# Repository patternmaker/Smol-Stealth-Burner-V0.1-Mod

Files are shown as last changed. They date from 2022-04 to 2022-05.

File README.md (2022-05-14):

# Smol-Stealth-Burner-V0.1-Mod
This Smol stealth burner does not lose any X,Y or Z travel. This means on stock V0.1 you don't need new bed mounts and you don't need to remove your stock bed. It has all best features I wanted in a Smol hotend without taking apart half your printer!
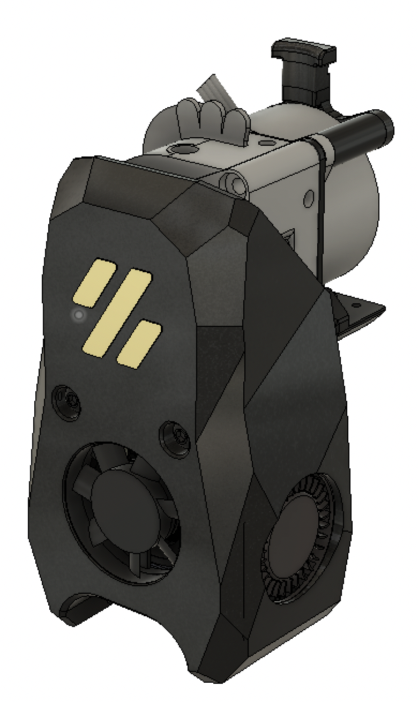
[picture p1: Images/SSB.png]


# License:
https://github.com/VoronDesign/Voron-0/blob/Voron0.1/LICENSE

I would say this is an intermediate build. You will need knowledge of soldering as well as wiring in general. You will need to work with small objects that can be a pain for unsteady hands. please keep this in mind.

# I AM NOT RESPONSIBLE FOR ANY DAMAGES TO YOUR PRINTER. PERFORM THIS MOD AT YOUR OWN RISK.

Print settings are standard Voron settings. The only exception is the X carraige. This will need support. There are two X carraige types. One with auto generated support and one without. I recommend printing the one without but if you don't trust your slicer use the one with. No way around it. You want the full x,y travel? Sacrafices have to be made. Don't worry its not a lot and should come off easy if they are dialed in.

# BOM
Currently ONLY LGX lite with dragon hotend or Voron Revo is supported if I have time I may help someone adapt other extruders and or hotends.

1. Two M3x35mm, Two M3x20mm socket or cap screws to screw in LGX Lite, two M2.5x4mm hotend mounting bolts socket or cap works.
2. A set of pogo pins. You will need to select. 4PIN SMD MALE AND FEMALE and I opted to buy more to have as spares testing I have no issues and they are rated to have enough to power the fans. https://www.aliexpress.com/item/1005003511237426.html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
3. A fine tip Soldering iron. Trust me this will not be fun without it.
4. Four 6x3mm magnets like all cool voron mods use.
5. Liquid electrical tape. Yes it is a thing.

# Steps for assemble cowling and mount with pogo pins.
  The magnets should have a press fit into the printed parts some might need glue from going too far in.
1. Make sure you have no connectors attached to your fans.
2.Start by feeding the cables through the channels I have made in the Cowling. Photos to show if your wires are too big cut them with some EXTRA INCASE YOU MESS UP. Dont worry there is plenty of space to hide them. :)
3. Cut a length of what you need to reach from the pogo pins to whatever setup your running. That means to reach your printer board. In the photos I am using the umbilical PCB by Timmit. Link: https://github.com/VoronDesign/Voron-Hardware/tree/master/V0-Umbilical I used approx 110mm of PTFE cable.
4. Tin the back side of the pogo pins. A little is all you need don't overdue it. The sides that do not have a spring pin or are indented. They should be FLAT.
5. Tin the negative and positive hotend fan ends. A little is all you need don't overdue it. Solder the hotend fan negative and positive two the back of pogo pins where you tinned. 
6. Twist both part cooling fan negatives wires together and repeat for positive. Tin these twisted wires. A little is all you need don't overdue it. Next Solder them to the two pins that are left on the pogo pins.. TO be on the safe side make sure negatives are next to each other so that if you are sloppy at least the wires are grounded.
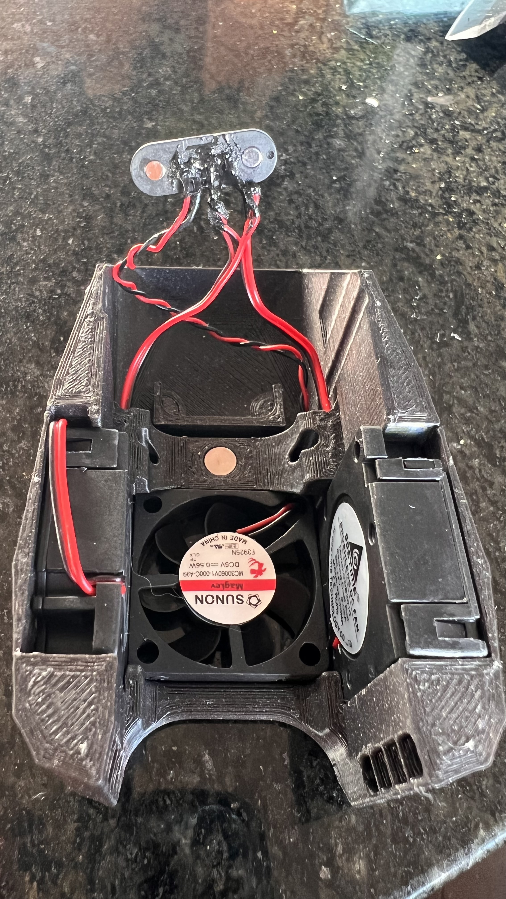
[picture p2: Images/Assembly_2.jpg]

8. Repeat these steps for the hotend mount side. Making sure to wire in one to one with the other. Meaning hotend fan positive lines up with hotend postive, Hotend negative lines with negative. Same goes for the part cooling fans. Double and triple Check. This is easy to mess up. Dont fry your poor 5v hotend fan.
9. Once you verified it is wired correctly Apply liquid electrical tape. This is for safety last thing we need is exposed wires and solder flying around at 100mm/s coming loose and touching. This seals but also insulates all your work.
10. Now these connectors should press in to the provided channels with the pogos facing each other.
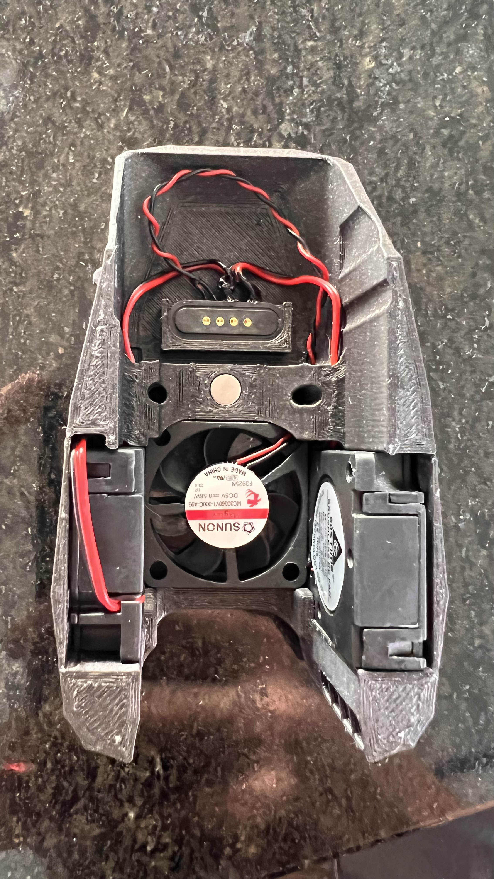
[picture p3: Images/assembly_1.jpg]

Voilà you now have an easy to work on hotend you have made it this far grab a cookie or take a drink.
They should pull to each other and make contact.

https://user-images.githubusercontent.com/79613562/166133340-f43cc9af-56ce-4bb5-8ee6-4b2d1e12f683.mov

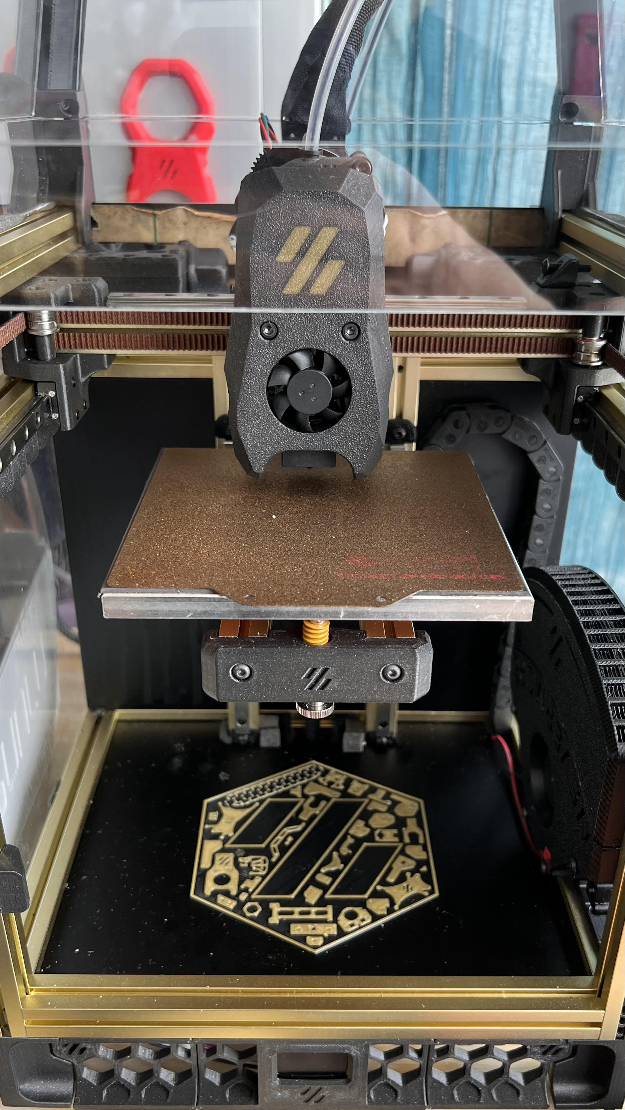
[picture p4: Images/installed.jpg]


Klipper does not like when certain things aren't connected so if you get an error make sure the pogos are connected when turning on your printer. Safety first klipper well done.
Thanks to @MAVERICK on discord for the inspiraion and guidance. Check out all the cool work he has done. https://github.com/PrintersForAnts/Crucible

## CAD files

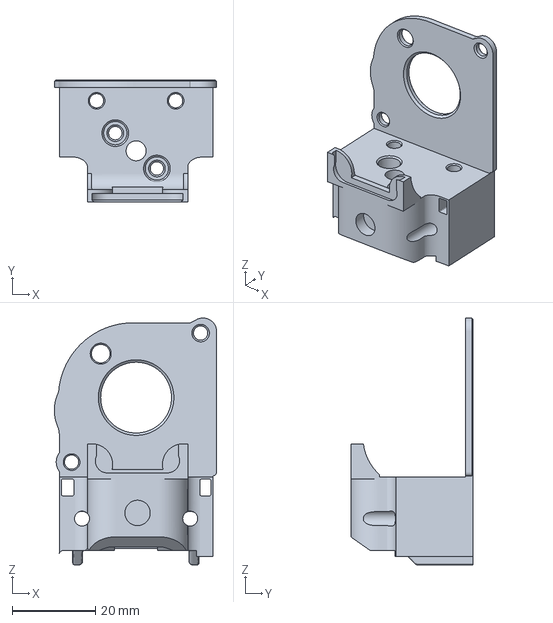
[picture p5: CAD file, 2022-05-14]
STLS/HOTEND_MOUNT_Revo_Voron-2.3mf
39.0 x 29.4 x 59.4 mm

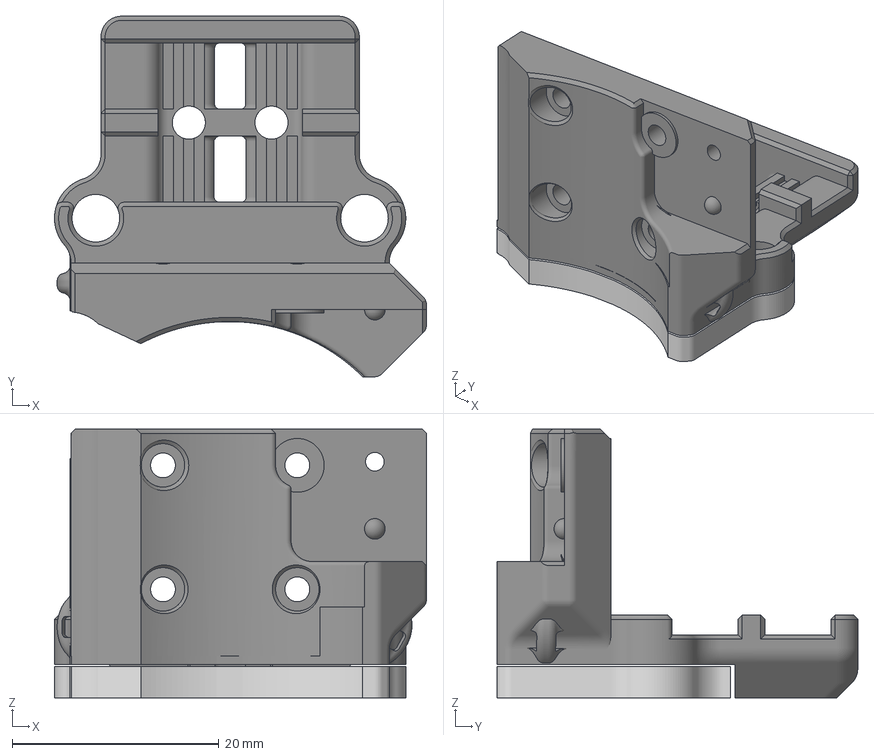
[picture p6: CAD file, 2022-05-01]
STLS/X_CARRIAGE_with_support.3mf
36.0 x 34.9 x 26.0 mm
X_CARRIAGE

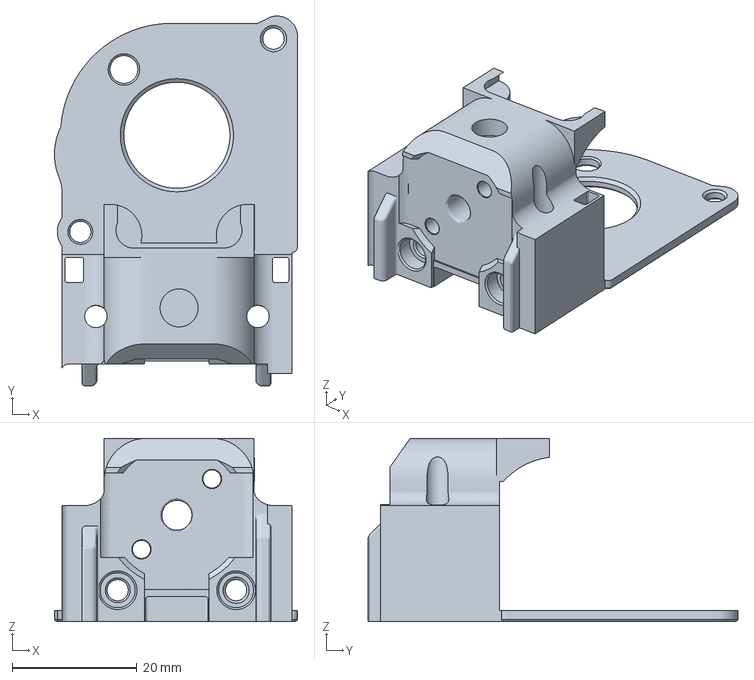
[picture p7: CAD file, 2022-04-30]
STLS/HOTEND_MOUNT_Dragon.3mf
39.0 x 59.4 x 29.4 mm

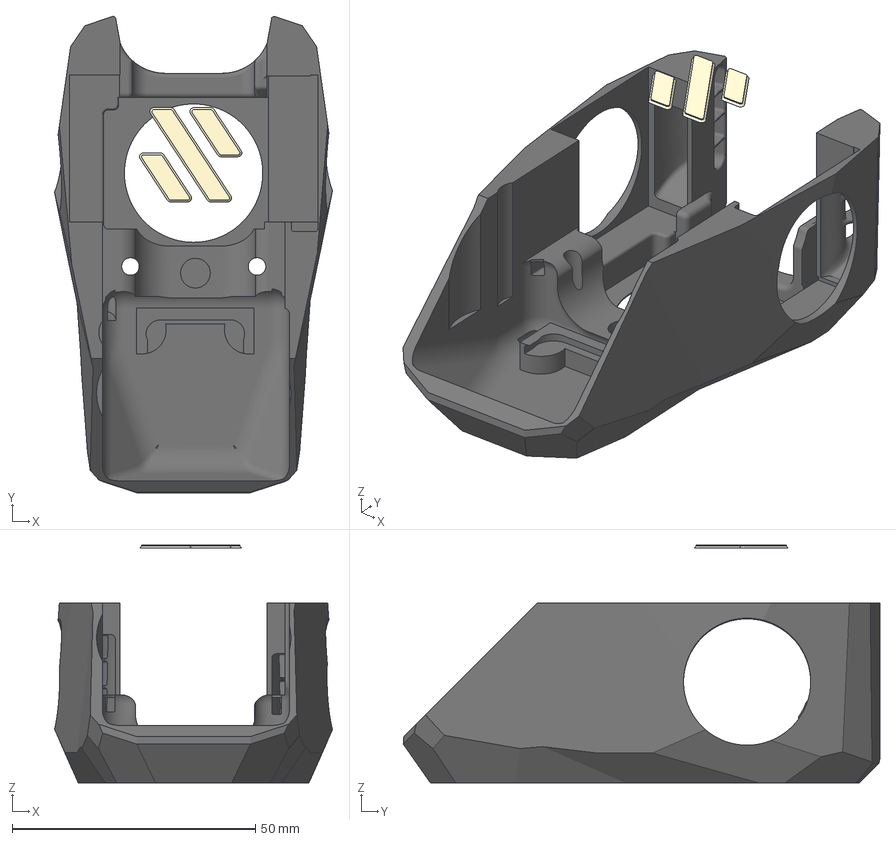
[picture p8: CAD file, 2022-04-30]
STLS/MAG_Cowling_POGO_dual_color.3mf
57.1 x 97.9 x 48.8 mm
COWLINGv2

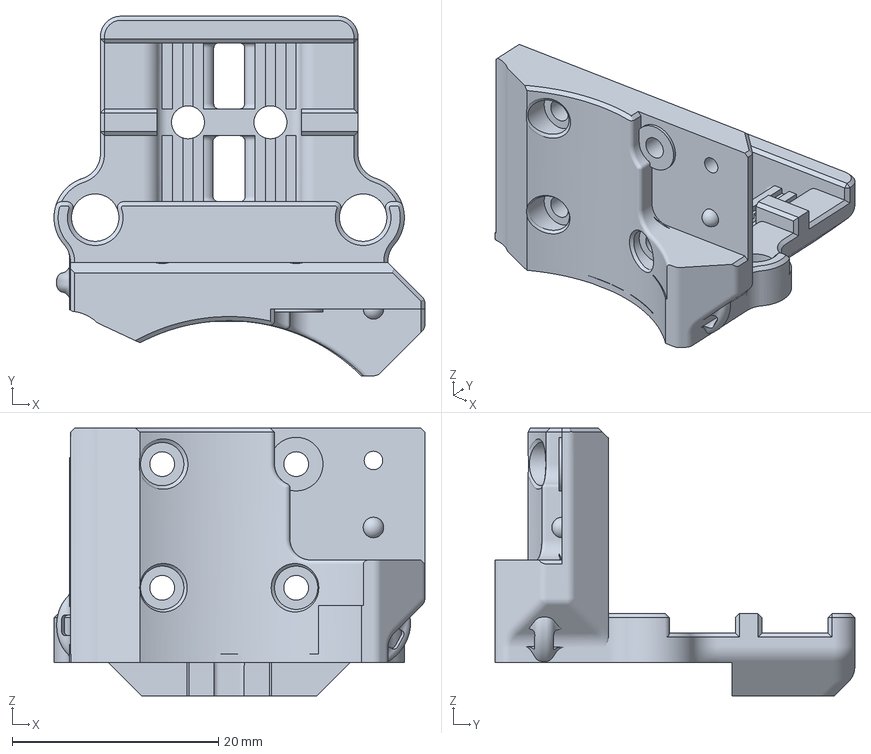
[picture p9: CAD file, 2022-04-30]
STLS/X_CARRIAGE_without_support.3mf
36.0 x 34.9 x 26.0 mm

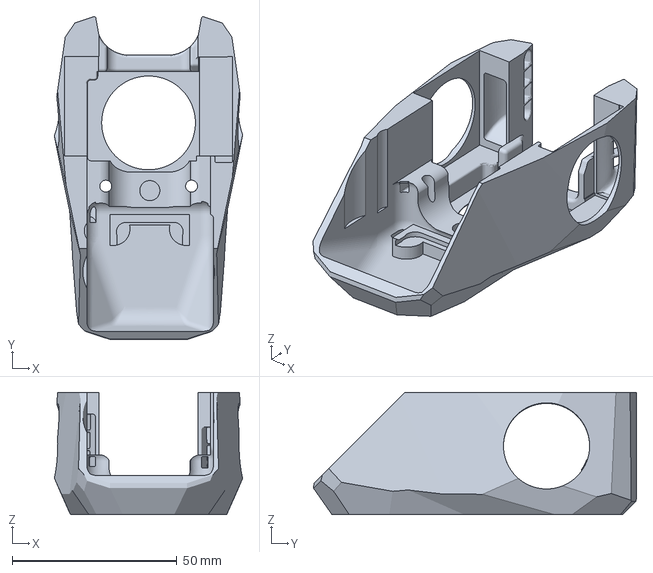
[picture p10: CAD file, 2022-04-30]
STLS/MAG_Cowling_POGO_single_color.3mf
57.1 x 97.9 x 37.0 mm

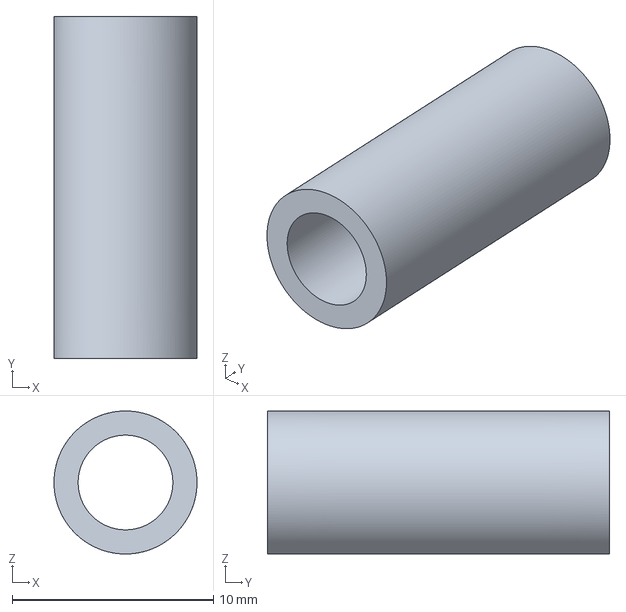
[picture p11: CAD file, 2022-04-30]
STLS/Spacer_20mm_x2.3mf
7.10 x 17.0 x 7.10 mm

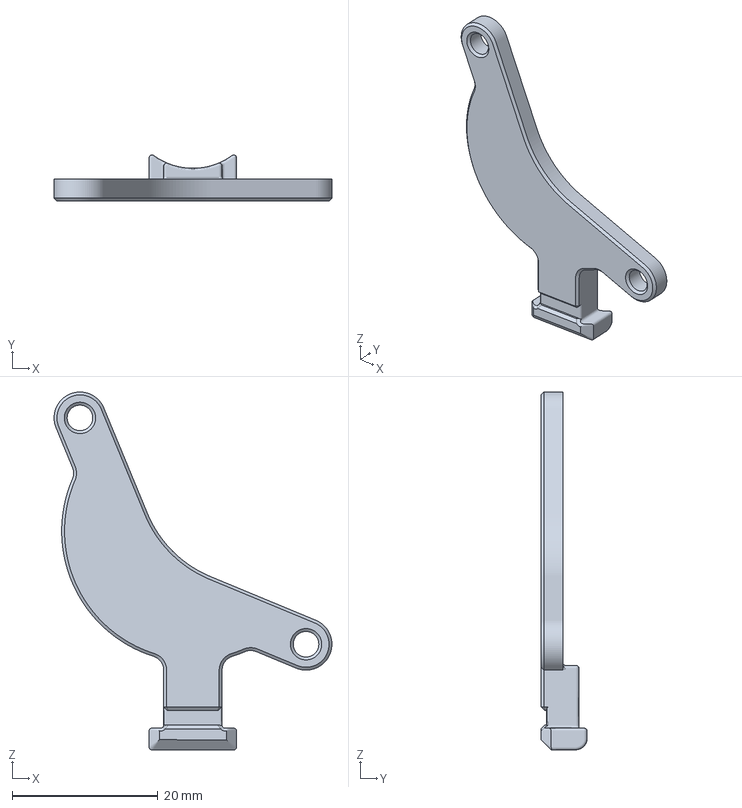
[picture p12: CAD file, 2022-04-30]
STLS/Strain_relief_LGX_lite.3mf
38.1 x 6.33 x 49.1 mm

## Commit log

2022-04-30 STLS
    ONLY X CARRIAGE NEEDS SUPPORT GENERATED
    [HOTEND_MOUNT Dragon.3mf, MAG Cowling POGO dual color.3mf, MAG Cowling POGO single color.3mf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]
2022-04-30 Create CAD files
2022-04-30 Create STL Files.md
2022-05-14 Add files via upload
    Adding support for Revo Voron edition.
    [HOTEND_MOUNT_Revo_Voron-2.3mf]
2022-05-14 Add files via upload
    Adding support for Voron Revo nozzle offset should be close to stock offset of dragon hot end when assembled. Reach out to me on discord @ pattern maker#1783 if the nozzle isn't close enough. I've had someone test fitment and they reported no issues.
    [HOTEND_MOUNT_Revo_Voron-2.3mf]
2022-05-19 Add files via upload
    Support for Zero click probe.
